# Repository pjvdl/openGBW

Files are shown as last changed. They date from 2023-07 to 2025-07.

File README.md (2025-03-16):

OpenGBW
=======

- [OpenGBW](#opengbw)
- [Differences to the original](#differences-to-the-original)
- [Dev environment setup](#dev-environment-setup)
- [Getting started](#getting-started)
- [Flashing firmware onto an ESP32](#flashing-firmware-onto-an-esp32)
- [Wiring](#wiring)
  - [Load Cell](#load-cell)
  - [Display](#display)
  - [Relay](#relay)
  - [Rotary Encoder](#rotary-encoder)
- [BOM](#bom)
- [3D Files](#3d-files)
- [Todo](#todo)
- [Troubleshooting](#troubleshooting)
  - [Can't upload](#cant-upload)

This Project extends and adapts the original by Guillaume Besson. It has been adapted to operate with a [ESP32-S3-DevKitC-1](https://docs.espressif.com/projects/esp-idf/en/latest/esp32s3/hw-reference/esp32s3/user-guide-devkitc-1.html) board.

**Note that the 3D base is designed to be used with a modified portafilter mount that must be fabricated from sheet stainless steel (1mm thick or similar). One possible design for this is included in the blender model.**

More info: https://besson.co/projects/coffee-grinder-smart-scale

This mod will add GBW functionality to basically any coffe grinder that can be started and stopped manually.

The included 3D Models are adapted to the Eureka Mignon XL, and Eureka Mignon Classico, but the electronics can be used for any Scale.

-----------

# Differences to the original

- changed IO pins to match [ESP32-S3-DevKitC-1](https://docs.platformio.org/en/latest/boards/espressif32/esp32-s3-devkitc-1.html) (44 pin) board
- updated 3D base to suit older Eureka Mignon (now known as the Mignon Classico) and to include mount points for electronic components
- The older Mignon doesn't include a 5V power supply, so we use a VREG7805 linear power regulator to take a 5V power supply from the 12V DC power, connected via a soldered 12V takeoff. We could use a buck converter here instead, but a linear converter is simpler and heat dissipation shouldn't be an issue with the small currents involved. 
- added a rotary encoder to select weight and navigate menus
- made everything user configurable without having to compile your custom firmware
- dynamically adjust the weight offset after each grind
- added relay for greater compatibility
- added different ways to activate the grinder
- added scale only mode

-----------

# Dev environment setup

Setup PlatformIO in VSCode as per OS specific instructions.

Note that this project is designed to be built/uploaded/monitored with the PlatformIO toolchain, rather than the ESP-IDF tools (via the PlatformIO extension navigation page).

USB cable can be connected to the USB or UART ports for upload, but should be plugged into the UART port for the serial monitor (ie. serial.println) to output to the serial terminal.

# Getting started

1) 3D print the included models for a Eureka Mignon XL or design your own
2) flash the firmware onto an ESP32 (see below)
3) connect the display, relay, load cell and rotary encoder to the ESP32 according to the wiring instructions
4) go into the menu by pressing the button of the rotary encoder and set your initial offset. -2g is a good enough starting value for a Mignon XL
5) if you're using the Mignon's push button to activate the grinder set grinding mode to impulse. If you're connected directly to the motor relay use continuous.
6) if you only want to use the scale to check your weight when single dosing, set scale mode to scale only. This will not trigger any relay switching and start a timer when the weight begins to increase. If you'd like to build your own brew scale with timer, this is also the mode to use.
7) calibrate your load cell by placing a 100g weight on it and following the instructions in the menu
8) set your dosing cup weight
5) exit the menu, set your desired weight and place your empty dosing cup on the scale. The first grind might be off by a bit - the accuracy will increase with each grind as the scale auto adjusts the grinding offset

-----------

# Flashing firmware onto an ESP32

This project is designed to be built on VSCode using the PlatformIO plugin. Install VSCode, the plugin and any prerequisites.

The [platformio.ini](./platformio.ini) file defines the build configurations. Build the default esp32_usb configuration for a standard runtime. The debug configuration can be used to debug the firmware.

To build and deploy:

1) Navigate to the PlatformIO IDE from the plugin navigation sidebar
2) Expand the build configuration that you want to use and select Build
3) Once built, upload to the esp32 via the USB port on the esp32 (UART port also works?)

If you want to debug, preform the same steps using the debug configuration. The install and configuration of the PlatformIO plugin and project should have created a number of standard VSCode debug configurations.

1) Build debug
2) Upload debug
3) F5 to run the debug configuration of your choice

-----------

# Wiring

## Load Cell

| Load Cell  | HX711 | ESP32  |
|---|---|---|
| black  | E-  | |
| red  | E+  | |
| green  | A+  | |
| white  | A-  | |
| | VCC  | VCC/3.3 |
| | GND  | GND |
| | SCK  | GPIO 7 |
| | DT  | GPIO 6 |

## Display

| Display | ESP32 |
|---|---|
| VCC | VCC/3.3 |
| GND | GND |
| SCL | GPIO 17 |
| SDA | GPIO 18 |

## Relay

| Relay | ESP32 | Grinder |
|---|---|---|
| + | VCC/3.3 | |
| - | GND | |
| S | GPIO 14 | |
| Middle Screw Terminal | | push button |
| NO Screw Terminal | | push button |

## Rotary Encoder

| Encoder | ESP32 |
|---|---|
| VCC/+ | VCC/3.3 |
| GND | GND |
| SW | GPIO 42 |
| DT | GPIO 41 |
| CLK | GPIO 40 |

-----------

# BOM

1x ESP32-S3-DevKitC-1  
1x HX711 load cell amplifier  
1x 1.3" OLED Display  
1x KY-040 rotary encoder  
1x 500g load cell 47 x 12 x 6mm
1x VREG7805 

various jumper cables  
a few WAGO or similar connectors

-----------

# 3D Files

You can find the 3D STL models on thangs.com

Eureka XL: https://thangs.com/designer/jbear-xyz/3d-model/Eureka%20Mignon%20XL%20OpenGBW%20scale%20addon-834667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

These _should_ fit any grinder in the Mignon line up as far as I can tell.

There's also STLs for a universal scale in the repo, though it is mostly meant as a starting off point to create your own. You can use the provided files, but you'll need to print an external enclosure for the ESP32, relay and any other components your setup might need.

# Todo

- ~add option to change grind start/stop behaviour. Right now it pulses for 50ms, this works if its hooked up to the push button of a Eureka grinder. Other models might need constant input while grinding~ done
- add mounting options and cable routing channels to base
- more detailed instructions (with pictures!)
- other grinders?
- ???

# Troubleshooting

## Can't upload

 I now found in one of the espressif docs that I need to press the BOOT button and if that doesn't help, keep the BOOT button pressed and press the RST button as well.

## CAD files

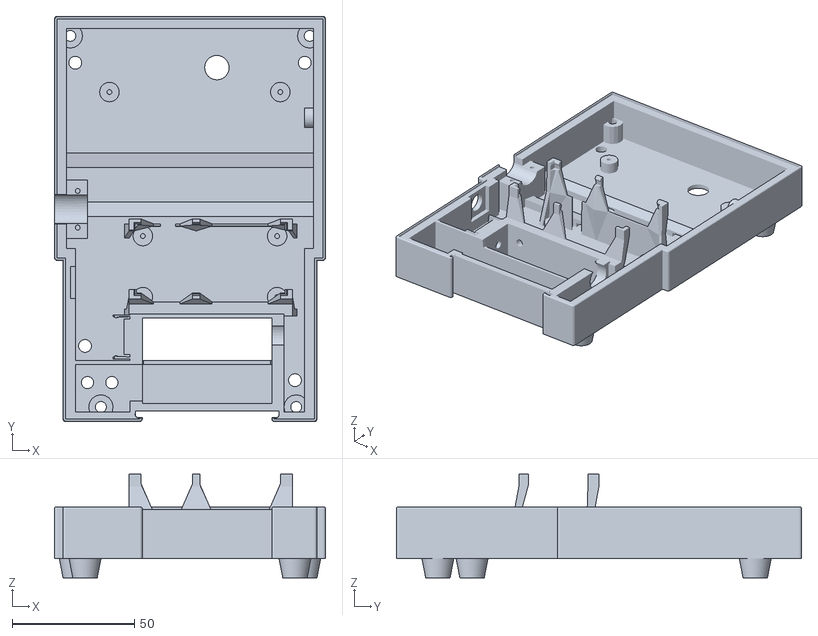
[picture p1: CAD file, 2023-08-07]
3D/Mignon/eureka_mignon_base.stl
111.0 x 166.0 x 42.5

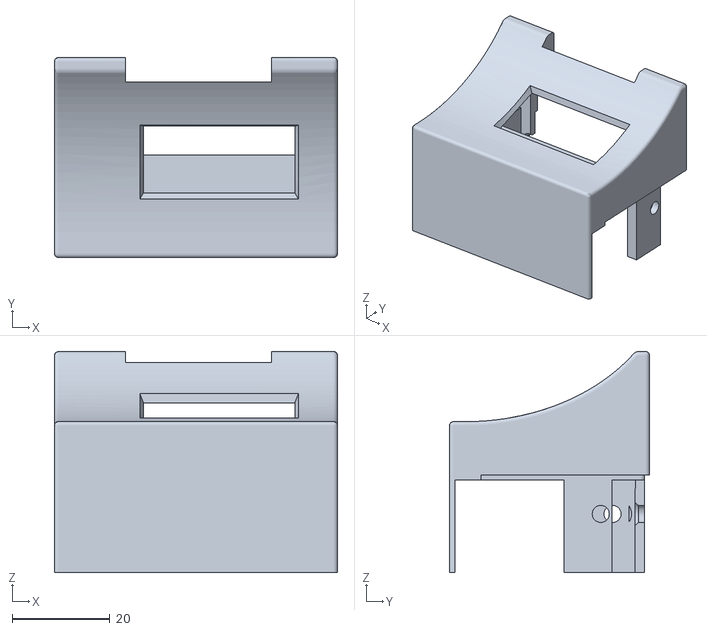
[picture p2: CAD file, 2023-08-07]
3D/Mignon/eureka_mignon_display_mount.stl
58.0 x 41.0 x 45.3

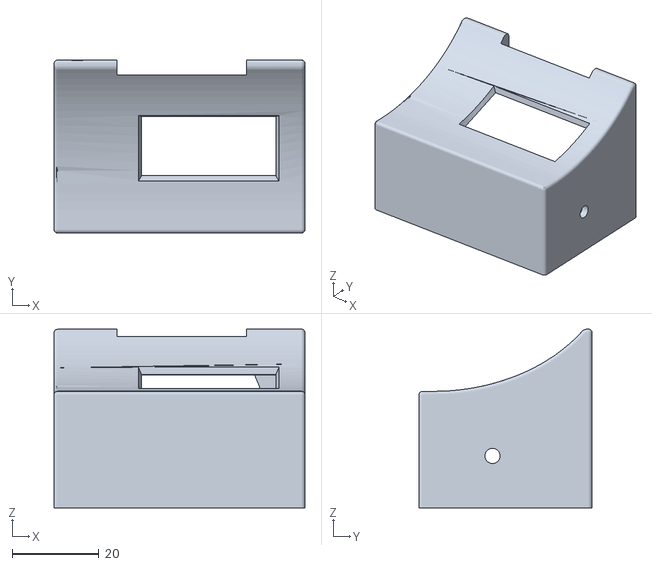
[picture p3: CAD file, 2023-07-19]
3D/Mignon/eureka_mignonDisplay_mount_curved.stl
58.0 x 40.0 x 41.3

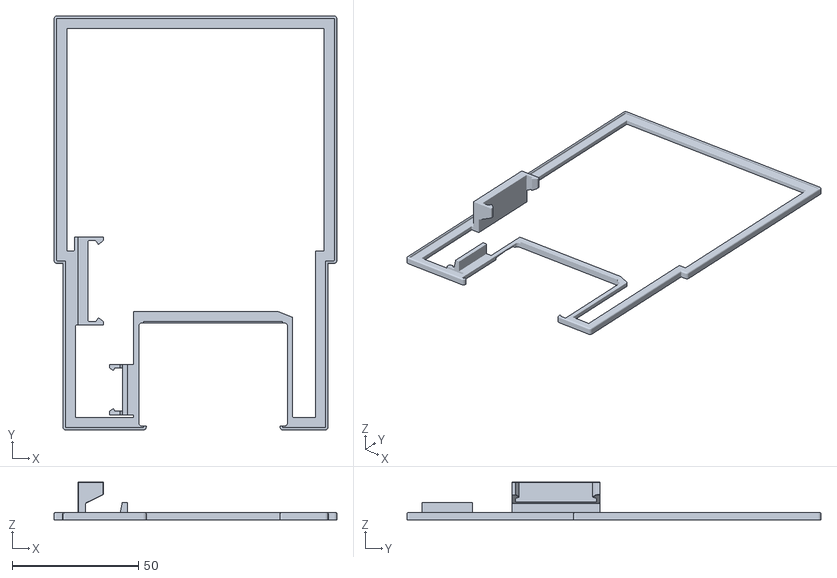
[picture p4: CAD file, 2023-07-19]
3D/Mignon/eureka_mignon_sliceScale_base_curved.stl
112.0 x 164.0 x 15.0

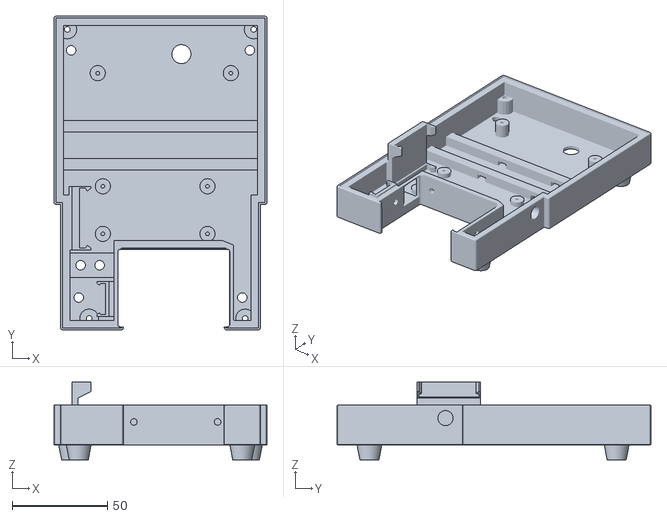
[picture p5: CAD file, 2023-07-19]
3D/Mignon/eureka_mignonScale_base_curved.stl
112.0 x 165.0 x 41.0

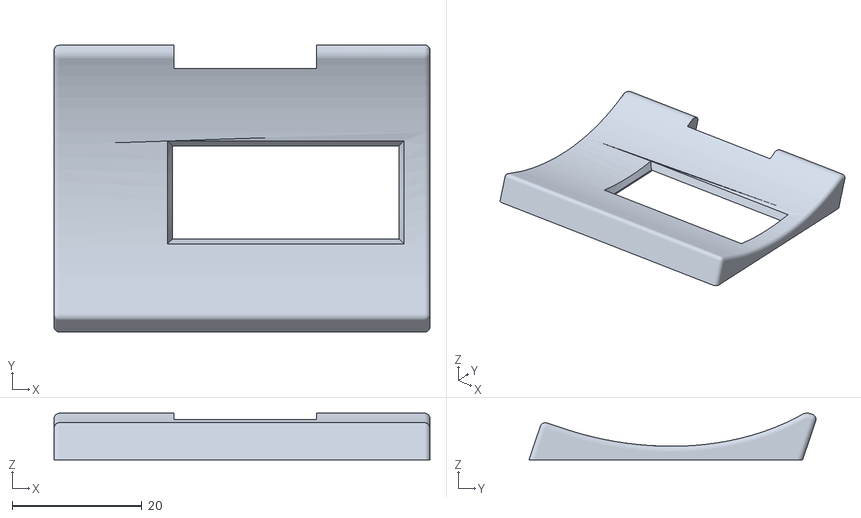
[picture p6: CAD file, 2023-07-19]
3D/Mignon/eureka_mignon_sliceDisplay_mount_curved.stl
58.0 x 44.3 x 7.22

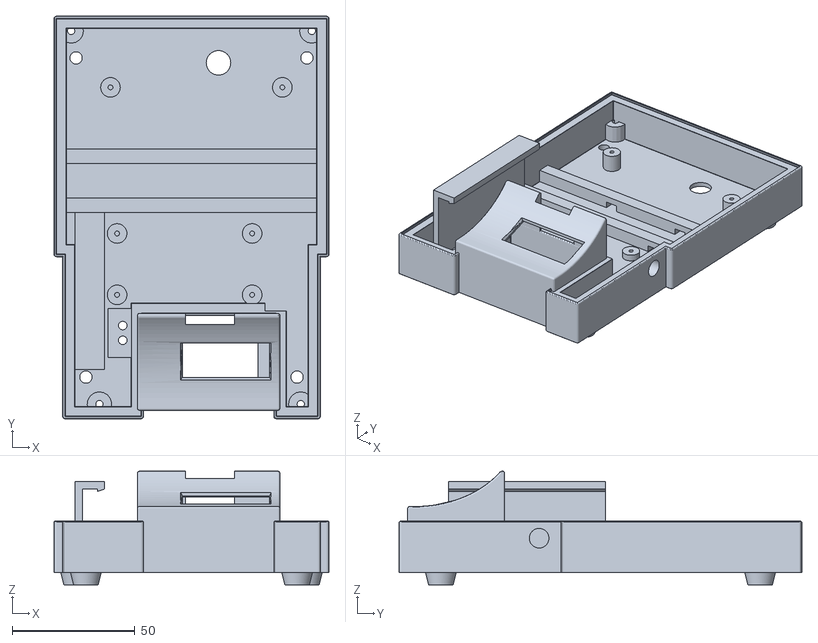
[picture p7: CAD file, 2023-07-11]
3D/Mignon/eureka_mignon.stl
112.0 x 164.0 x 46.3

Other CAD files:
3D/Mignon/eureka_mignon.blend
3D/Mignon/eureka_mignon_slice.blend

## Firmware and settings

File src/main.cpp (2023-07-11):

#include <Arduino.h>
#include <WiFi.h>
#include <PubSubClient.h>


#include "display.hpp"
#include "scale.hpp"

WiFiClient espClient;
PubSubClient client(espClient);

//wifi not used for now. Maybe OTA later
const char *ssid = "ssid"; // Change this to your WiFi SSID
const char *password = "pw"; // Change this to your WiFi password
long lastReconnectAttempt = 0;


void setup() {


  /* Print chip information */
  esp_chip_info_t chip_info;
  uint32_t flash_size;
  esp_chip_info(&chip_info);
  printf("This is %s chip with %d CPU core(s), %s%s%s%s, ",
          CONFIG_IDF_TARGET,
          chip_info.cores,
          (chip_info.features & CHIP_FEATURE_WIFI_BGN) ? "WiFi/" : "",
          (chip_info.features & CHIP_FEATURE_BT) ? "BT" : "",
          (chip_info.features & CHIP_FEATURE_BLE) ? "BLE" : "",
          (chip_info.features & CHIP_FEATURE_IEEE802154) ? ", 802.15.4 (Zigbee/Thread)" : "");

  unsigned major_rev = chip_info.revision / 100;
  unsigned minor_rev = chip_info.revision % 100;
  printf("silicon revision v%d.%d, ", major_rev, minor_rev);
  if(esp_flash_get_size(NULL, &flash_size) != ESP_OK) {
      printf("Get flash size failed");
      return;
  }

  printf("%" PRIu32 "MB %s flash\n", flash_size / (uint32_t)(1024 * 1024),
          (chip_info.features & CHIP_FEATURE_EMB_FLASH) ? "embedded" : "external");

  printf("Minimum free heap size: %" PRIu32 " bytes\n", esp_get_minimum_free_heap_size());

  Serial.begin(115200);
  while(!Serial){
    delay(50);
  }
  Serial.println("Serial line initialised");
  printf("Hello world!\n");
  
  
  setupDisplay();
  setupScale();

  Serial.println();
  Serial.println("******************************************************");
  // Serial.print("Connecting to ");
  // Serial.println(ssid);

  // WiFi.begin(ssid, password);

  // while (WiFi.status() != WL_CONNECTED) {
  //   delay(500);
  //   Serial.print(".");
  // }

  // Serial.println("");
  // Serial.println("WiFi connected");
  // Serial.println("IP address: ");
  // Serial.println(WiFi.localIP());
  // lastReconnectAttempt = 0;
  // client.setServer("192.168.1.201", 1883);
}

boolean reconnect() {
  if (client.connect("coffee-scale")) {
    // Once connected, publish an announcement...
    Serial.println("Connected to MQTT");
  }
  return client.connected();
}

void loop() {
  // if (!client.connected()) {
  //   long now = millis();
  //   if (now - lastReconnectAttempt > 5000) {
  //     lastReconnectAttempt = now;
  //     // Attempt to reconnect
  //     if (reconnect()) {
  //       lastReconnectAttempt = 0;
  //     }
  //   }
  // } else {
  //   client.loop();
  // }
  //rotary_loop();
  delay(1000);
}

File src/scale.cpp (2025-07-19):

#include "scale.hpp"
#include <MathBuffer.h>
#include <AiEsp32RotaryEncoder.h>
#include <Preferences.h>

HX711 loadcell;
SimpleKalmanFilter kalmanFilter(0.02, 0.02, 0.01);

Preferences preferences;


AiEsp32RotaryEncoder rotaryEncoder = AiEsp32RotaryEncoder(ROTARY_ENCODER_A_PIN, ROTARY_ENCODER_B_PIN, ROTARY_ENCODER_BUTTON_PIN, ROTARY_ENCODER_VCC_PIN, ROTARY_ENCODER_STEPS);

#define ABS(a) (((a) > 0) ? (a) : ((a) * -1))

TaskHandle_t ScaleTask;
TaskHandle_t ScaleStatusTask;

double scaleWeight = 0; //current weight
double calibrationFactor = 1; // current calibration of scale
bool wakeDisp = false; //wake up display with rotary click
double setWeight = 0; //desired amount of coffee
double setCupWeight = 0; //cup weight set by user
double offset = 0; //stop x grams prios to set weight
bool scaleMode = false; //use as regular scale with timer if true
bool grindMode = true;  //false for impulse to start/stop grinding, true for continuous on while grinding
bool grinderActive = false; //needed for continuous mode
MathBuffer<double, 100> weightHistory;

unsigned long lastAction = 0;
unsigned long scaleLastUpdatedAt = 0;
unsigned long lastTareAt = 0; // if 0, should tare load cell, else represent when it was last tared
bool scaleReady = false;
bool calibrationError = false;
int scaleStatus = STATUS_EMPTY;
double cupWeightEmpty = 0; //measured actual cup weight
unsigned long startedGrindingAt = 0;
unsigned long finishedGrindingAt = 0;
int encoderDir = -1;
bool greset = false;

bool newOffset = false;

int currentMenuItem = 0;
int currentSetting;
int encoderValue = 0;
int menuItemsCount = 8;
MenuItem menuItems[8] = {
    {MENU_ITEM_MANUAL_GRIND, false, "Manual Grind", 0},
    {MENU_ITEM_CUP_WEIGHT, false, "Cup weight", 1, &setCupWeight},
    {MENU_ITEM_CALIBRATE, false, "Calibrate", 0},
    {MENU_ITEM_OFFSET, false, "Offset", 0.1, &offset},
    {MENU_ITEM_SCALE_MODE, false, "Scale Mode", 0},
    {MENU_ITEM_GRINDING_MODE, false, "Grinding Mode", 0},
    {MENU_ITEM_EXIT, false, "Exit", 0},
    {MENU_ITEM_RESET, false, "Reset", 0}}; // structure is mostly useless for now, plan on making menu easier to customize later

void grinderToggle()
{
  if(!scaleMode){
    if(grindMode){
      grinderActive = !grinderActive;
      digitalWrite(GRINDER_ACTIVE_PIN, grinderActive);
    }
    else{
      digitalWrite(GRINDER_ACTIVE_PIN, 1);
      delay(100);
      digitalWrite(GRINDER_ACTIVE_PIN, 0);
    }
  }
}


void rotary_onButtonClick()
{
  wakeDisp = 1;
  lastAction = millis();

  if(dispAsleep)
    return;

  if(scaleStatus == STATUS_EMPTY){
    scaleStatus = STATUS_IN_MENU;
    currentMenuItem = MENU_ITEM_MANUAL_GRIND;
    rotaryEncoder.setAcceleration(0);
  }
  else if(scaleStatus == STATUS_OFFSET_WARNING){
    scaleStatus = STATUS_IN_SUBMENU;
    currentSetting = MENU_ITEM_OFFSET;
    Serial.println("Offset Menu from Warning");
    rotaryEncoder.setAcceleration(0);
  }
  else if(scaleStatus == STATUS_MANUAL_IN_PROGRESS) {
    grinderToggle();
    scaleStatus = STATUS_GRINDING_FINISHED;
    finishedGrindingAt = millis();
    Serial.println("Finished Grinding");
  }
  else if(scaleStatus == STATUS_IN_MENU){
    if(currentMenuItem == MENU_ITEM_EXIT){
      scaleStatus = STATUS_EMPTY;
      rotaryEncoder.setAcceleration(100);
      Serial.println("Exited Menu");
    }
    else if (currentMenuItem == MENU_ITEM_MANUAL_GRIND)
    {
      // grinderToggle();
      scaleStatus = STATUS_MANUAL_READY;
      currentSetting = MENU_ITEM_MANUAL_GRIND;
      Serial.println("Manual Grind Menu");
    }
    else if (currentMenuItem == MENU_ITEM_OFFSET){
      scaleStatus = STATUS_IN_SUBMENU;
      currentSetting = MENU_ITEM_OFFSET;
      Serial.println("Offset Menu");
    }
    else if (currentMenuItem == MENU_ITEM_CUP_WEIGHT)
    {
      scaleStatus = STATUS_IN_SUBMENU;
      currentSetting = MENU_ITEM_CUP_WEIGHT;
      Serial.println("Cup Menu");
    }
    else if (currentMenuItem == MENU_ITEM_CALIBRATE)
    {
      scaleStatus = STATUS_IN_SUBMENU;
      currentSetting = MENU_ITEM_CALIBRATE;
      Serial.println("Calibration Menu");
      printPreferencesToSerial();
    }
    else if (currentMenuItem == MENU_ITEM_SCALE_MODE)
    {
      scaleStatus = STATUS_IN_SUBMENU;
      currentSetting = MENU_ITEM_SCALE_MODE;
      Serial.println("Scale Mode Menu");
    }
    else if (currentMenuItem == MENU_ITEM_GRINDING_MODE)
    {
      scaleStatus = STATUS_IN_SUBMENU;
      currentSetting = MENU_ITEM_GRINDING_MODE;
      Serial.println("Grind Mode Menu");
    }
    else if (currentMenuItem == MENU_ITEM_RESET)
    {
      scaleStatus = STATUS_IN_SUBMENU;
      currentSetting = MENU_ITEM_RESET;
      greset = false;
      Serial.println("Reset Menu");
      printPreferencesToSerial();
    }
  }
  else if(scaleStatus == STATUS_IN_SUBMENU){
    if(currentSetting == MENU_ITEM_OFFSET){

      preferences.begin("scale", false);
      preferences.putDouble("offset", offset);
      preferences.end();
      scaleStatus = STATUS_IN_MENU;
      currentSetting = MENU_ITEM_NONE;
    }
    else if (currentSetting == MENU_ITEM_CUP_WEIGHT)
    {
      if(scaleWeight > 30){       //prevent accidental setting with no cup
        setCupWeight = scaleWeight;
        Serial.println(setCupWeight);
        
        preferences.begin("scale", false);
        preferences.putDouble("cup", setCupWeight);
        preferences.end();
        scaleStatus = STATUS_IN_MENU;
        currentSetting = MENU_ITEM_NONE;
      }
    }
    else if (currentSetting == MENU_ITEM_CALIBRATE)
    {
      calibrateScale();
      scaleStatus = STATUS_IN_MENU;
      currentSetting = MENU_ITEM_NONE;
    }
    else if (currentSetting == MENU_ITEM_SCALE_MODE)
    {
      preferences.begin("scale", false);
      preferences.putBool("scaleMode", scaleMode);
      preferences.end();
      scaleStatus = STATUS_IN_MENU;
      currentSetting = MENU_ITEM_NONE;
    }
    else if (currentSetting == MENU_ITEM_GRINDING_MODE)
    {
      preferences.begin("scale", false);
      preferences.putBool("grindMode", grindMode);
      preferences.end();
      scaleStatus = STATUS_IN_MENU;
      currentSetting = MENU_ITEM_NONE;
    }
    else if (currentSetting == MENU_ITEM_RESET)
    {
      if(greset){
        preferences.begin("scale", false);
        preferences.putDouble("calibration", (double)LOADCELL_SCALE_FACTOR);
        setWeight = (double)COFFEE_DOSE_WEIGHT;
        preferences.putDouble("setWeight", (double)COFFEE_DOSE_WEIGHT);
        offset = (double)COFFEE_DOSE_OFFSET;
        preferences.putDouble("offset", (double)COFFEE_DOSE_OFFSET);
        setCupWeight = (double)CUP_WEIGHT;
        preferences.putDouble("cup", (double)CUP_WEIGHT);
        scaleMode = false;
        preferences.putBool("scaleMode", false);
        grindMode = true;
        preferences.putBool("grindMode", true);
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

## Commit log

2023-06-18 fixed submenu coder direction
    [scale.cpp]
2023-07-04 Adapt to ESP32-S3-DevKitC-1
2023-07-11 Adapt for ESP32-S3-DevKitC-1 board and add PlatformIO debug configuration
    [eureka_mignon.blend, eureka_mignonScale_base.stl]
2023-07-11 Minor changes to 3D models
    [eureka_mignon.blend, eureka_mignon.stl, eureka_mignonScale_base.stl]
2023-07-19 3D models updates for Mignon
    [eureka_mignon_slice.blend]
2023-07-19 3D model updates for Mignon
    [eureka_mignon.blend, eureka_mignonDisplay_mount_curved.stl, eureka_mignonScale_base_curved.stl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]
2023-08-07 Tweeks to 3D model and failure modes
    [eureka_mignon.blend, eureka_mignon_base.stl, eureka_mignon_display_mount.stl]
2023-08-14 timing changes for failures
    [eureka_mignon.blend]
2025-07-19 offset warning and fixes to taring
    [scale.cpp, scale.hpp]
